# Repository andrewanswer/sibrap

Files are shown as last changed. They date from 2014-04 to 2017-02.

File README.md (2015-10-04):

СИБРАП - СИБИРСКАЯ РЕАЛИЗАЦИЯ РЕПРАП
31 марта 2012 - ...

О проекте
---------

Проект представляет собой 3D-принтер, позволяющий создавать
трехмерные объекты из пластика по его 3D-модели. Данный проект
был создан на базе проекта RepRap http://reprap.org и принтера Gen X
http://skb-kiparis.ru. Все файлы данного проекта выпущены под
лицензией GPL v3 (см. файл license_ru.txt).

Официальный сайт проекта - http://livelyminds.ru (Гибкие умы)

Об авторах
----------

Андрей Нуждов http://answe.ru
Будет дополняться...

Поддержка проекта
-----------------

Любой желающий поддержать проект анонимно либо публично может
перечислить любую сумму на следующие реквизиты:

Yandex.Money 4100171308229

WebMoney WMR R367868798166
         WMZ Z377208196018

Во втором случае он будет упомянут в списке жертвователей,
который будет включен в данный репозиторий проекта.

Развитие проекта
----------------

Все желающие помочь проекту делом, материалами или инструментами...
Если вы хотите открыть мастерскую, производящую Сибрапы, и вам
нужны консультации...
Если у вас есть вопросы и пожелания авторам...

пишите на http://livelyminds.ru/contact

==============================================================
SIBRAP - REPRAP SIBERIAN IMPLEMENTATION

About project
-------------

This project is a 3D-printer which allow to create real things
from plastic based on 3D-model. This project derived from RepRap
http://reprap.org and Gen X http://skb-kiparis.ru.
All this project files published under GPL v3 license
(see license_en.txt).

Official project site - http://livelyminds.ru (Lively Minds)

About authors
-------------

Andrew (Answer) Nuzhdov http://andrew.answer.name
Will be continued...

Project support
---------------

Anyone who want to support project (donate money) anonymously, or public,
can use next payment systems:

Yandex.Money 4100171308229

WebMoney WMR R367868798166
         WMZ Z377208196018

BitCoin  1qYeAD3AQgpYTpsLHjsZDKReWE29sTL8z
PayPal   andrew@answer.name

Second case sender will be included into list of donors
published in this repository.

Project expansion
-----------------

If you want to help project with any sort of activity, materials and tools...
If you try to open SibRaps foundry and want to consult...
Ii you have questions and wishes...

write to http://livelyminds.ru/contact

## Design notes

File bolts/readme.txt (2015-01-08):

BOLTS library have NUTS, WASHERS and HEX bolts, but doesn't exist bolts with cross-round head.
Here is it (MCAD OpenScad metric_fastners library used).

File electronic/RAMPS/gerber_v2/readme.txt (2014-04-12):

RAMPS_1-41.do  - Dimensions
RAMPS_1-41.GTL - TOP Copper
RAMPS_1-41.GBL - BOTTOM Copper
RAMPS_1-41.GTS - Solder stop mask Top
RAMPS_1-41.GBS - Solder stop mask Bottom
RAMPS_1-41.GTO - Silk Top
RAMPS_1-41.GBO - Silk Bottom
RAMPS_1-41.TXT - Drill

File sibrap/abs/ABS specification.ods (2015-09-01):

 |  |  | Часть принтера | Новое название |  | Название в sibrap_upgrade | Название в sibrap-kit | Кол-во деталей | Файл .scad | Файл .stl | Кол-во распечаток | Деталей внутри STL | Файл .gcode | Деталей внутри gcode
L | 1 | 4 | Каретка | carriage-part01 | x | Направляющие по оси Z | Направляющие (детали каретки X) | 1 | 1-rightbottom | 1-rightbottom | 1 | 1
L | 2 |  | Каретка | carriage-part02 | x |  |  | 1 | 2-leftbottom | 2-leftbottom | 1 | 1
L | 3 |  | Каретка | carriage-part03 | x |  |  | 1 | 3-righttop | 3-righttop | 1 | 1
L | 4 |  | Каретка | carriage-part04 | x |  |  | 1 | 4-lefttop | 4-lefttop | 1 | 1
S | 5 | 6 | Рама | frame-part01 | x | Зажим направляющих | Ушки | 4 | - | Зажим направляющих | 1 | 1
S | 6 |  | Рама | frame-part02 | x | Концевики | Крепления концевых датчиков | 3 | part23 | part23 | 3 | 1
S | 7 |  | Рама | frame-part03 | x | Прижим Z | Зажимы направляющих Z | 4 | part06 | part06 | 4 | 1
S | 8 |  | Рама | frame-part04 | x |  | Зависит от толщины рамы! | 4 | part06_1 | part06_1 | 4 | 1
S | 9 |  | Рама | frame-part05 | x | Хомут М5 | Хомуты М5 | 4 | - | Хомут М5 | 4 | 1
S | 10 |  | Рама | frame-part06 | x | Рама — Держатель кнопки | Печатать, только если нет в БП! | 1 | - | Держатель кнопки | 1 | 1
L | 11 | 8 | Головка-экструдер | head-part01 | x | Каретка экструдера | Головка экструдера | 1 | Экструдер_3_7 | Экструдер_3_7 | 1 | 1
M | 12 |  | Головка-экструдер | head-part02 | x | Экструдер — меньшая деталь | Головка экструдера | 1 | part18_new | part18_new | 1 | 1
S | 13 |  | Головка-экструдер | head-part03 | x | Экструдер — крышечка | Головка экструдера | 1 | part19 | part19 | 1 | 1
M | 14 |  | Головка-экструдер | head-part04 | x | Шестерни — большая (metal-bolt) | Редуктор большая шестерня | 1 | gear_large_42_teeth | gear_large_42_teeth | 1 | 1
S | 15 |  | Головка-экструдер | head-part05 | x | Шестерни — малая | Редуктор малая шестерня | 1 | gear_small_hole | gear_small_hole_4 | 1 | 1
S | 16 |  | Головка-экструдер | head-part06 | x | Каретка экструдера — шпуля 22 зуба | Натяжитель экструдера | 1 | Шпуля-GT2_22-зуба | Шпуля-GT2_22-зуба | 1 | 1
S | 17 |  | Головка-экструдер | head-part07 | x | Прижим разъема экструдера | Держатель разъема Molex | 1 | part16_molex | part16_molex | 1 | 1
S | 18 |  | Головка-экструдер | head-part08 | x | Прижим болта | Барашек | 1 | - | Барашек | 1 | 1
M | 19 | 5 | Катушка-вентилятор | holder-part01 | x | Держатель катушки | Держатель катушки | 2 | - | d3 | 2 | 1
M | 20 |  | Катушка-вентилятор | holder-part02 | x |  | Зависит от толщины рамы! | 1 | - | d2-v2 | 1 | 1
M | 21 |  | Катушка-вентилятор | holder-part03 | x |  | Зависит от толщины рамы! | 1 | - | d1-v3-rotated | 1 | 1
M | 22 |  | Катушка-вентилятор | holder-part04 | x | - | Крепление вентилятора | 1 | - | d5-v2 | 1 | 1
M | 23 |  | Катушка-вентилятор | holder-part05 | x |  | Зависит от толщины рамы! | 1 | - | d4-v2 | 1 | 1
M | 24 | 2 | Стол | table-part01 | x | Ножки | Ножки стола | 4 | part22 | part22 | 4 | 1
S | 25 |  | Стол | table-part02 | x | Зажимы ремня столика GT2 | Ремень стола | 9 | part12_gt2 | part12_gt2 | 3 | 3
 |  |  |  |  |  |  | Итого | 51
S — Small, M — Medium, L — Large
Постобработка деталей — сверла, диаметр
3 | 5 | 8 | base_plate01 | 1
3 |  |  | base_plate02 | 1
3 | 8 |  | base_plate03 | 1
4 | 5 | 8 | base_plate04 | 1
2 | 3 | 8 | carriage-part01 | 1
2 | 3 | 8 | carriage-part02 | 1
2 | 3 | 8 | carriage-part03 | 1
2 | 3 | 8 | carriage-part04 | 1
3 |  |  | head-part01 | 1
3 | 5 |  | head-part02 | 1
 |  |  | head-part04 | 1
 |  |  | ИТОГО | 11

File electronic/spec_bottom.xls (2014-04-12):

После заполнения спцификации, строки выделенные этим цветом желательно удалить, так как они не содержат необходимой для монтажа информации | Что необходимо предоставить при заказе на монтаж ПП
 | 1. Заполненный бланк заказа на монтаж
 | 2. Полный список комплектующих по заказу.( по Образцу)
 | 3. Список комплектующих по каждой стороне ПП: отдельно по SMD компонентам (с указанием типа корпуса )
 | и компонентам монтируемым в отверстия ПП. Наименование компонента в списке должно соответствовать
 | сборочному чертежу.
 | 4. На сборочном чертеже обязательно указать ориентацию полярных компонентов и микросхем.
 | 5. Сборочный чертеж должен быть понятен и хорошо читаем.
 | 6. При повторном заказе предоставлять список изменений.
Образец списка комплектующих |  | Ячейки выделенные желтым цветом обязательно заполнить
Организация | Название платы | Ответственное лицо, телефон |  | Кол-во плат
частное лицо | Плата 1984 | Нуждов А.А. 79232464120 |  | 50
Номинал | Позиционное обозначение | Тип | Дополнительная информация | Кол-во | Паек | Примечания
Компоненты для монтажа на поверхность
Резисторы
1.1 кОм | R1 | SMD 0805 | Резистор 0.125 W, SMD | 1 | 2
NTC 100 кОм | R2 | SMD 0805 | терморезистор 0.125 W, SMD | 1 | 2
Светодиоды
RED LED | D1 | SMD 0805 | Светодиод красный | 1 | 2
 |  |  | Всего SMD компонентов | 3
 |  |  | Всего паек SMD компонентов |  | 6
Компоненты для монтажа в отверстия
Разъемы
ножевая клемма на плату | J1-2 | TA-M | ножевая клемма | 2 | 4
2-pin угловой | X1 | MW-2MR | 2-pin угловой | 1 | 2
 |  |  | Всего монтир. в отверс. Компонентов | 3
 |  |  | Всего паек монт. в отв. компонентов |  | 6
Телефон: (383) 316-53-57 |  |  | E-mail: marlang@ngs.ru

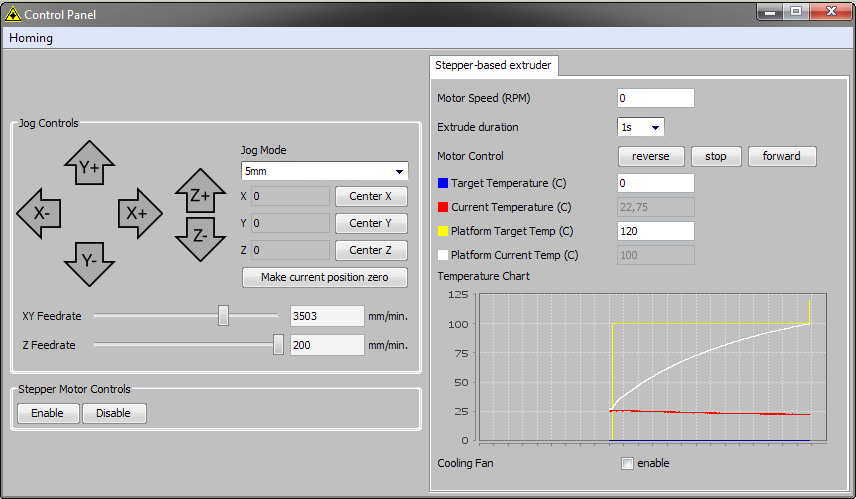
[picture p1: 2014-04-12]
electronic/kiparis-mytable.png

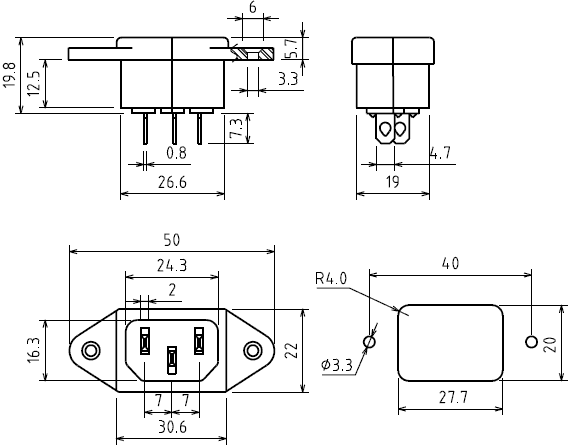
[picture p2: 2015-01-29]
specs/ac220v.gif

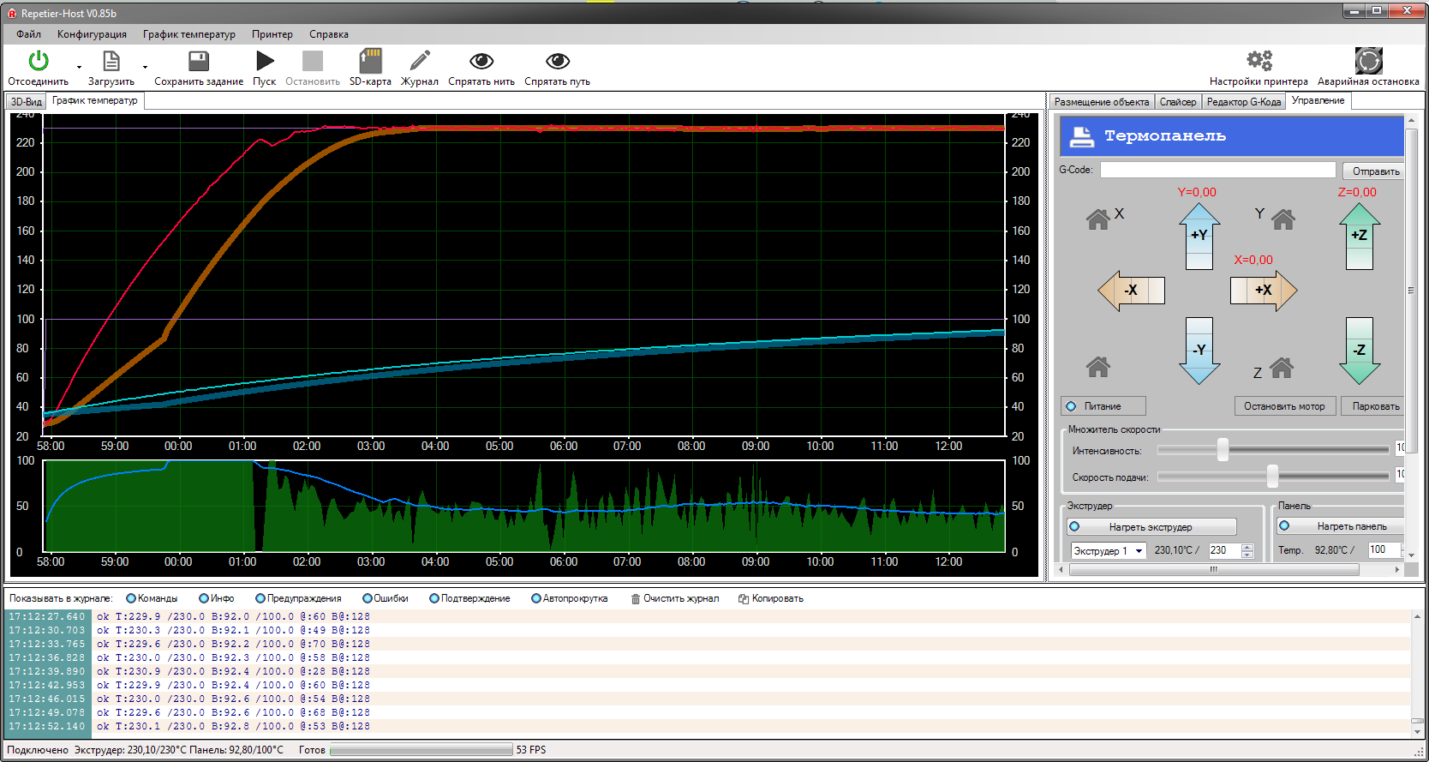
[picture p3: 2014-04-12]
electronic/ramps-mytable.png

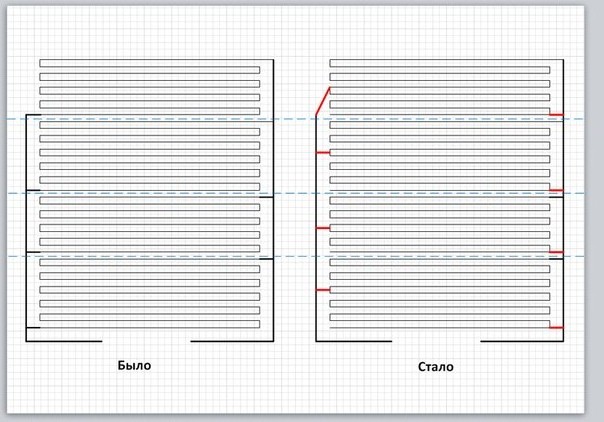
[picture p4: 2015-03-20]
electronic/table-update.jpg

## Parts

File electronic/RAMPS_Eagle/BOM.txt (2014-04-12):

Bill of Materials from RAMPS_1-41_n.sch, 88 parts, grouped by values, as of 21.06.2013 23:26:14

Part									Qty	Value			Device			Package			Description
5V, PS-ON, VCC								3	 			PINHD-1X1		1X01			Pin header 1x1 for 0.1" spacing
12V-AUX									1	 			M02PTH			1X02			Header 2
A-OUT, E0-MOT, E1-MOT, I2C, SERIAL, X-MOT, Y-MOT, Z-MOT, Z-MOT1		9	 			PINHD-1X4		1X04			PIN HEADER
C1, C5, C8								3	10uF			CPOL-US153CLV-0405	153CLV-0405		POLARIZED CAPACITOR, American symbol
C2									1	100nF			C-EUC0805		C0805			CAPACITOR, European symbol
C3, C4, C6, C7, C9, C10							6	100uF			CPOL-US153CLV-0605	153CLV-0605		POLARIZED CAPACITOR, American symbol
D1, D2									2	1N4004			1N4004			DO41-10			DIODE
F1									1	MFR500			PTCFUSE			MFR500			LITTLEFUSE
F2									1	MFR1100			PTCFUSEMFR1100		MFR1100			LITTLEFUSE
JP2, JP3, JP4, JP5, JP6							5	 			PINHD-2X3		2X03			PIN HEADER
JP7									1	 			M06SIP			1X06			Header 6
LED1, LED2, LED3, LED4							4	 			LEDCHIP-LED0805		CHIP-LED0805		LED
LOGO1									1	OSHW_LOGO_6MILX0100-NT	OSHW_LOGO_6MILX0100-NT	OSHW_6X100_NOTEXT
Q1, Q2, Q3								3	STP55NF06L		IRF512			TO220BV			N-CHANNEL MOS FET
R1, R7, R11, R21, R22							5	4.7K			R-US_R0805		R0805			RESISTOR, American symbol
R2, R3, R4, R5, R6, R8, R9, R10						8	100k			R-US_R0805		R0805			RESISTOR, American symbol
R12									1	1K			R-US_R0805		R0805			RESISTOR, American symbol
R13, R15								2	10r			R-US_R0805		R0805			RESISTOR, American symbol
R14									1	10r			R-US_M0805		M0805			RESISTOR, American symbol
R16, R17, R18, R19, R20							5	10k			R-US_R0805		R0805			RESISTOR, American symbol
R23, R24, R25								3	1.8K			R-US_R0805		R0805			RESISTOR, American symbol
S1									1	 			31-XX			B3F-31XX		OMRON SWITCH
SER1, SER2, SER3, SER4, X+, X-, Y+, Y-, Z+, Z-				10	 			3PIN-HEADER		3PIN-HEADER		PIN HEADER
U$2									1	282837-6		282837-6		282837-6
U$3									1	M04X2			M04X2			2X4
U$4, U$5, U$6, U$7, U$8							5	A4988BREAKOUT		A4988BREAKOUT		A4988BREAKOUT
U$9									1	M18_			M18_			1X18
U$10									1	M05X2			M05X2			2X5
U1									1	ARDUINO_MEGA_SHIELD	ARDUINO_MEGA_SHIELD	ARDUINO_MEGA_SHIELD
X4									1	MSTBA4			MSTBA4			MSTBA4			PHOENIX

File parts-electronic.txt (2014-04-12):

Электроника: поставщики

купили 21 ноября, доставили 25 ноября
Электронная плата основная 5000 р
Нагревательный элемент в сборе 1300 р
+ доставка через http://www.edostavka.ru 1000 р -

СКБ Кипарис http://skb-kiparis.ru
г.Москва, г.Зеленоград, корп. 1130
+7 (916) 754-99-29
+7 (926) 549-52-27
mail@skb-kiparis.ru

Разъемы, резисторы для нагревательного эл-та, разъем для подложки в
Радиотовары, Иванова, 17 (383) 336-05-26 http://novoelectronica.ru
(подложка - плата-теплый стол)

В начале ноября (примерно 3 ноября) ездили на оценку пр-ва электроники.
Оценка производства плат по файлам с разводкой -
Электроконнект, Инженерная, 4
(383) 336-10-01
(383) 336-10-03
order@pselectro.ru

Подложка:
10 шт = 8565 р
12 шт = 7980 р
24 шт = 11905 р

Gen6-электроника:
через калькулятор http://pselectro.ru/calc/
1 шт = 3269 р
10 шт = 4978 р
20 шт = 5714 р

реально, через беседу в офисе по макету
100 шт = 25000 р
10 шт = 7000 р
1 шт - ручная пайка = 10000 р
Контакт: Елена, (383) 316-53-57, marlang@ngs.ru

=====================================================
Элементы для подложки:
термистор
резистор
светодиод
=====================================================
Альтернативная электроника см REPRAP

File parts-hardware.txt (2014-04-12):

Железные детали, крепеж: поставщики

купили 7 ноября

Ремни Optibelt зубчатые
316XL 6,35 мм 4 шт * 158 р/шт + НДС 18% = 745 р
XL 6,35 мм 5 метров длиной, белый 1 шт * 1681 р + НДС 18% = 1983 р
Итого 2728 р, без доставки

Поставщик ЗИП-Балтика, Новосибирск
сайт http://e-zip.ru
(383) 325-34-12
(383) 233-05-11
(383) 325-34-13

купили 9 ноября

Двигатели 4 шт
Шаговый двигатель FL42STH38-1206A 4 шт * 928 р/шт + НДС 18% = 4380 р
+ доставка 1000 р = 5380 р

Поставщик ЗАО Меджик-Системс, Санкт-Петербург
сайт http://stepmotor.ru stepmotor@magicsys.spb.ru
(812) 327-13-88 доб 106
(812) 953-07-32
(812) 716-45-72

==============================================
Направляющие 6шт * 8мм диаметр * 400мм длиной выточил Владимир, обошлись в 1500 руб
Стержни 8мм с резьбой М8 можно купить в любом строительном магазине и нарезать их ножовкой
Все гайки, винты можно купить в магазине крепежа АкадемГородок ул. Иванова, 31 (383) 36-35-725
Латунный пруток для экструдера и нагревательного элемента купили в Бердске на пункте приема цветного металла
Фторопласт?
Подшипники?
Чертежи вручную выточенных деталей?
==============================================
Направляющие:
http://www.purelogic.ru/Netshop/linperem/cillinper/polival/ (от 10 мм)
http://electroprivod.ru/linear-guide-r.htm (на 8 мм есть но от 500 мм длины)
http://russian.alibaba.com/product-gs/standard-linear-shaft-8mm-540354747.html (Китай)
==============================================
Фторопласт, капролон (вместо бронзовых втулок можно сделать капролоновые)
http://www.rtigrupp.ru/ РЕЗИНОТЕХНИКА
(383) 363-27-01 (383) 363-27-02  ул. Толмачевская, 43/1
Там же можно купить гетинакс/стеклотекстолит для корпуса электроники
==============================================
Латунь
http://www.suet-metal.ru/cvetnoy-metal/latunnuy.htm
http://metacolor-nsk.ru/content/latun/
http://metalloprokat-scs.ru/czvetnoj-metall/latun-prokat/kvadrat-latunnyij.html
==============================================

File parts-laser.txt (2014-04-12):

Детали из оргстекла: поставщики, лазерная резка, файлы

19 октября
пришли детали для 3D принтера.
Файл parts-laser.cdr

оргстекло 665*322 мм, толщина 18 мм:
1 держатель маленький 24 шт
2 ножка-держатель 10 шт
3 загогулина верхняя 6 шт
4 держатель для мотора Z 5 шт
6 зажим для направляющей 8 шт
13 держатель для мотора Y 3 шт
17 каретка экструдера, самая большая деталь 3 шт
20 каретка площадки 2 шт

30 ноября
пришли детали для 3D принтера.
Файл parts2-laser.cdr (10 мм), остальное поштучно

оргстекло 180*180 мм, толщина 10мм:
16 большие шестерни экструдера 43 зуба 3 шт
10,11 шестерни на ось Z (справа и слева одинаковые) 8 шт

+ оргстекло 18мм, остатки предыдущего распила:
9 малые шестерни экструдера 10 зубов 3 шт
8 шестерни на ось X/Y 6 шт
5 держатели для концевиков 10 шт

========================================
Оргстекло (нужно 18 мм и 8 мм) можно купить тут
http://www.bis077.ru/catalog/goods/id/50255

ТД Пластик-Н ООО возле Автокомбината (Петухова Хилокский рынок)
г. Новосибирск, ул. Троллейная, д. 87 к4, оф. 2, эт. 2
тел. (383) 291-12-58 (383) 240-96-97
Оргстекло техническое, ТОСП, ТОСН, т.18мм, 1500х1700мм, литьевое, г. Новосибирск
Под заказ

18мм 1400x1620 15200 вес 60кг
раб время 9-17

Оргстекло техническое, ТОСП, ТОСН, т.8мм, 1500х1700мм, литьевое
5670 руб за лист, вес 26.5 кг
адрес? 

(звонить пн-пт 9-17)
или тут (www.termahim.ru/)
========================================
Нарезать можно тут
http://l-plast.ru/ (или http://www.siblaser.ru/)
(383)286-65-97 (383)299-68-10 Бердск, Линейная, 5/2

НО лучше всего тут Мазак Лазер т.к. по карте близко к ТД Пластик
лист можно повезти сразу к ним
http://www.m-lazer.ru/contacts/ ул. Сибиряков-Гвардейцев, 56 (383) 362-05-01

Кстати, лазерный б/у станок, который продается тут (http://l-plast.ru/ 9060SC) 
стоит относительно недорого -- новый стоит 200 тысяч 
http://cnc.ruprom.net/p39859-lazernyj-stanok-rabbit.html
Чаще всего выходит из строя лампа, стоит 20 тысяч
http://www.all-ready.ru/komplektuyuschie-lazernogo-oborudovaniya
========================================
Еще интересное наблюдение: схема бизнеса на 3д-принтерах в целом повторяет схему
бизнеса на лазерных станках:
1) продажа самих станков
2) продажа услуг по резке/печати
3) продажа продукции собственного изготовления (эксклюзивный дизайн вещи + резка/печать)

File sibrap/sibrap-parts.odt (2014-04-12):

Допилы деталей из оргстекла

Деталь 1 — держатель маленький

- развернуть отверстие на 8
- просверлить и развернуть перпендикулярное отверстие на высоте 7 от основания, симметрично осевой линии

Деталь 2 — ножка

- развернуть два отверстия на 8
- просверлить и развернуть два отверстия — в изогнутой верхней части на расстоянии 8 от края симметрично осевой линии, и на высоте 38 мм снизу симметрично осевой линии

Деталь 3 — загогулина верхняя

- развернуть два отверстия на 8
- просверлить и развернуть два отверстия — в изогнутой верхней части на расстоянии 9 от угла симметрично осевой линии

Деталь 4 — держатель для мотора Z

Две детали

4.1 — для двигателя. Нужно:

- высверлить 4 отверстия диаметром 3 для крепежа мотора
- нарезать резьбу М5 в двух отверстиях сбоку
- просверлить и развернуть два сквозных отверстия на 8 сбоку

4.2 — для держателя подшипника. Нужно:

- профрезеровать цилиндр под подшипник глубиной 7,6 мм и диаметром 22 мм
- нарезать резьбу М5 в 4х отверстиях для крепежа подшипника
- нарезать резьбу М5 в двух отверстиях сбоку
- просверлить и развернуть два сквозных отверстия на 8 сбоку

В случае двух двигателей нужны 2 детали 4.1

Деталь 5 — концевик

Деталь 6 — зажим для направляющей Z

- просверлить два отверстия диаметром 5 сбоку на расстоянии 16 друг от друга и симметрично осевой линии

Деталь 13 — держатель для мотора Y

Деталь 14 — держатель для мотора X

Деталь 15 — держатель каретки

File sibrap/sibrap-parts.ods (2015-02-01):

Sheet: SibRap 6
Принтер SibRap версия 6 (1.4)
Отличия:
 | - рама из 4х деталей (оргстекло 18мм)
 | - линейные подшипники LM8UU по всем осям вместо бронзовых втулок
 | - практически все 3д-печатные детали переделаны
 | - площадка под столом из алюминия вместо фанеры
 | - ремень Y теперь крепится иначе
 | - изменились длины шпилек и направляющих
 | - вместо муфт ставится резиновая трубка и хомуты
 | - по вертикали теперь шпилька М5
№ | Название | Хар-ки | Кол-во | Файл, примечания | Поставщик |  | Цена без учета доставки | Доставка | Примечание
1 | Двигатель | ST42-47 | 5
2 | Шкив ремня X,Y | На вал 5 мм, 20 зубов | 2
3 | Ремень зубчатый метражом | GT2 6,35 мм x 1,8 м | 1 | см. ниже расклад
4 | Направляющая | 400 мм длина, 8 мм диаметр | 4
4 | Направляющая | 434 мм длина, 8 мм диаметр | 2
5 | Линейные подшипники LM8UU | 8 внутр х 15 внеш х 24 длина | 12
6 | Шпилька резьбовая | М8, длина 324 мм | 4 | Рама
7 | Шпилька резьбовая | М5, длина 330 мм | 2 | Ходовые валы
 | Шпилька резьбовая | М8, длина 210 мм | 1 | Держатель катушки
 | Шпилька резьбовая | М8, длина 135 мм | 1 | Держатель катушки
 | Шпилька резьбовая | М8, длина 155 мм | 1 | Держатель катушки
8 | Рама из оргстекла | Оргстекло 18 мм | 1 | laser/frame/v2/blocks/frame_final
7 | Гайка с фланцем | М8 | 0 | см. ниже расклад
8 | Гайка обычная | М8 | 2 | см. ниже расклад
9 | Гайка удлиненная | М5 | 0 | см. ниже расклад
10 | Винт подшипника для ремня X | М8 х 30 | 2 | см. ниже расклад
11 | Шайбы обычные | М8 | 9 | см. ниже расклад
12 | Шайбы кузовные | М8 х 30 наружный диаметр | 6 | см. ниже расклад
13 | Винты с внутр шестигранником | М5 х 16 | 8 | см. ниже расклад
14 | Винты с внутр шестигранником, крепление корпуса | М5 х 10 | 8 | см. ниже расклад
15 | Винты для крепления площадки | М4 х 35 потайная | 4 | см. ниже расклад
16 | Гайки с сальником для площадки и сборки корпуса | М4 | 4 | см. ниже расклад
17 | Винт | М3 | 77 | см. ниже расклад
18 | Гайка | М3 | 55 | см. ниже расклад
19 | Винты для крепления корпуса | М4 х 10 полукруг крест | 12
20 | Корпус | Сталь 1,5 мм, 4 детали | 1
21 | Уголки | бытовые, 13мм до центров отверстий, диам отв 4 | 12
22 | Подшипник | 8 внутр х 22 внеш х 7 высота | 8 | см. ниже расклад
 |  |  |  | ftoroplast/
24 | Фторопластовая шайба |  | 1 | extruder-part01
25 | Фторопластовый термобарьер |  | 1 | extruder-part02
26 | Фторопластовый переходник 3 мм 1.75 мм |  | 1 | extruder-part07
 |  |  |  | metal/
27 | Нагревательный элемент | Латунь, 20х15х10 мм | 1 | extruder-part03
28 | П-швеллер | Алюминий, 20 (хвосты) х 25 (перекладина) х 36 мм (длина) | 1 | extruder-part04
29 | Латунное сопло |  | 1 | extruder-part05
30 | Болт с резьбовой канавкой | M8 x 60, резьба на хвосте 23 мм, шестигранная головка | 1 | extruder-part06
31 | Втулка для крышки головки | Алюминиевая трубка, диаметр 8, длина 12 мм | 1 | -
32 | Площадка под стол | Алюминий 3 мм | 1 | metal/alum_table/table-3mm-aluminium
33 | Радиатор | Алюминиевый охладитель — переделан |  | metal/alum_radiator
 |  |  |  | laser/
40 | Держатель для мотора Y | Оргстекло 8 мм | 1 | part13
41 | Держатель подшипника каретки | Оргстекло 8 мм | 1 | part14
42 | Держатель для мотора X | Оргстекло 8 мм | 1 | part15
 |  |  |  | abs/
44 | Держатель разъема | ABS-пластик, печатать слоем 0.3 мм | 1 | part16
45 | Головка, большая деталь | ABS-пластик, печатать слоем 0.3 мм | 1 | part17
46 | Головка, средняя деталь | ABS-пластик, печатать слоем 0.3 мм | 1 | part18
47 | Головка, крышечка | ABS-пластик, печатать слоем 0.3 мм | 1 | part19
48 | Держатель концевых переключателей | ABS-пластик, печатать слоем 0.3 мм | 3 | part23
49 | Втулка пластиковая для бронзовых втулок | ABS-пластик, печатать слоем 0.3 мм | 20 | part11
50 | Держатель ремня площадки | ABS-пластик, печатать слоем 0.3 мм | 6 | part12
51 | Редуктор, большая шестерня | ABS-пластик, печатать слоем 0.3 мм | 1 | gears/gear_large
52 | Редуктор, малая шестерня | нейлон, печатать слоем 0.3 мм | 1 | gears/gear_small
53 | Стекло | 210 х 210 х 4 мм с отшлифованными краями | 1
 |  |  |  | table/
54 | СМЛ стол | Стекломагниевый лист 210 x 210 x 8 мм, обклеен бумагой с помощью строительного клея ПВА | 1 | table2
56 | Концевые переключатели | 3-х позиционные микропереключатели | 3
57 | Набор электроники RAMPS | FreeDuino, 4 StepStick, RAMPS | 1
58 | Плата стола | Изготовлена, список компонентов см ниже | 1
59 | Блок питания ATX | LW2-500W | 1
60 | Кулер охлаждающий | 8 х 8 см | 1
61 | miniUSB-кабель | 1,8 м | 1
62 | Резистор для нагрева | 8 Ом 1 Вт | 2
63 | Термистор | EPCOS NTC 100 кОм, проволочно-стеклянный, диаметр 2 мм | 1
64 | Провода | Метраж и диаметр см ниже | 1
Метраж зубчатых ремней: на ось X — 90 см, на ось Y — 90 см.
Распил из 2х метровых шпилек M8: |  |  | Остаток, мм
1 | 324+324+324 | 972 | 28
2 | 324+210+135+155 | 824 | 176
Расклад крепежа:
Винты М8x30 с полукруглой головкой |  | Крепление подшипников ремня X | 2
Гайки М8 с фланцем:
4 | Крепление шпилек к раме | 4 | 16
2 | Крепление ушек | 4 | 8
1 | Крепление подшипников Y и детали part13 | 6 | 6
1 | Крепление подшипников X к деталям part14, part15 | 2 | 2
 |  | Итого | 32
Гайки М8 обычные:
1 | Крепление болта с канавкой к головке | 2 | 2
 |  | Итого | 2
Шайбы обычные M8:
4 | Для шкивов ремня Y
4 | Для шкивов ремня X
1 | Для большой шестерни на каретке
9 | Итого
Шайбы кузовные M8x30:
4 | Для шкивов ремня Y
2 | Для шкива ремня X
6 | Итого
Винты М5 с полукруглой головкой: |  | Длина, мм
2 | Сборка рамы | 50
2 | Сборка рамы | 60
Винты М5 с внутренним шестигранником: |  | Длина, мм
4 | Крепление направляющих Z | 35
4 | Крепление направляющих Z | 30
8 | Итого
Гайки M5 нейлон:
4 | Сборка рамы
8 | Крепление направляющих Z
12 | Итого
Гайки удлиненные M5:
2 | Ходовые гайки по Z
Шайбы М5:
4 | Сборка рамы
4 | Крепление направляющих Z
8 | Итого
Винты M4x35 потайная головка:
4 | Площадка стола
2 | Крепление вентилятора
6 | Итого
Гайки М4:
2 | Площадка стола | 4 | 8
2 | Крепление вентилятора | 1 | 2
 |  | Итого | 10
Гайки М4 нейлон:
1 | Площадка стола | 4 | 4
Шайбы M4:
3 | Площадка стола | 4 | 12
2 | Крепление вентилятора | 1 | 2
 |  | Итого | 14
Винты M3: |  | Длина, мм | Кол-во по длинам
4 | Крепление мотора X | 12 | 12 | 33
4 | Крепление мотора Y | 12 | 16 | 6
8 | Крепление моторов Z | 20 | 20 | 19
4 | Крепление мотора экструдера | 12 | 25 | 6
2 | Крепление скобы к мотору экструдера | 40/50 (зависит от мотора) | 30 | 3
1 | Крепление ремня X со стороны двигателя | 12 | 40 | 3
4 | Крепление линейных подшипников в каретке | 16 | 50 | 9
1 | Крепление ремня X со стороны головки | 16 | Итого | 79
3 | Крепление сопла к головке экструдера | 30
3 | Крепление головки к каретке | 50
1 | Прижим крышечки в головке экструдера | 16
4 | Крепление направляющих X (упор) | 12
8 | Крепление направляющих X (сжатие) | 20
16 | Крепление ножек к площадке стола | 12
3 | Крепление держателя концевых переключателей | 20
6 | Крепление ремня Y к столу | 25
4 | Крепление каретки XZ | 50
1 | Натяжитель ремня в столе | 40
77 | Итого
Гайки М3:
4 | Крепление линейных подшипников в каретке
2 | Крепление ремня X со стороны головки
3 | Крепление сопла к головке экструдера
3 | Крепление головки к каретке
1 | Прижим крышечки в головке экструдера
12 | Крепление направляющих X
16 | Крепление ножек к площадке стола
3 | Крепление держателя концевых переключателей
6 | Крепление ремня Y к столу
4 | Крепление каретки XZ
1 | Натяжитель ремня в столе
55 | Итого
Шайбы M3:
1 | Прижим крышечки в головке экструдера
8 | Крепление направляющих X
16 | Крепление ножек к площадке стола
3 | Крепление держателя концевых переключателей
6 | Крепление ремня Y к столу
8 | Крепление каретки XZ
1 | Натяжитель ремня в столе
43 | Итого
Винты М2:
6 | Крепление концевых переключателей
Гайки M2:
6 | Крепление концевых переключателей
Подшипники:
4 | Каретка экструдера
2 | Шкив ремня Y
2 | Шкив ремня X
8 | Итого
Длины проводов: |  | Длина, мм | Кол-во жил | Сечение жилы, мм2 | Кол-во выводов на разъемы RAMPS | Кол-во выводов на клеммы RAMPS
 | Концевик X | 600 | 2 | 0,35 | 2 | 0
 | Концевик Y | 700 | 2 | 0,35 | 2 | 0
 | Концевик Z | 600 | 2 | 0,35 | 2 | 0
 | Кулер | 600 | 2 | 0,35 | 0 | 2
 | Мотор X | 400 | 4 | 0,35 | 4 | 0
 | Мотор Y | 500 | 4 | 0,35 | 4 | 0
 | Мотор Z1 (над X) | 200 | 4 | 0,35 | 4 | 0
 | Мотор Z2 | 400 | 4 | 0,35 | 4 | 0
 | Мотор E | 900 | 4 | 0,35 | 4 | 0
 | Сопло S | 1100 | 4 | 0,35 | 2 | 2
 | От сопла до разъема | 100 | 4 | 0,35 | 0 | 0
в наборе | Стол датчик | 900 | 2 | 0,35 | 2 | 0
в наборе | Стол нагрев | 800 | 2 | 2,5 | 0 | 2
есть в БП | Блок питания | 450 | 4 | 0,35 | 0 | 4
 |  |  |  |  | 30 | 10
Итого |  | в принтере |  | в наборе
2-жильный 0,35 мм2 |  | 3400 | т. е. 4 метра | 2500 | т. е. 3 метра
2-жильный 2,5 мм2 |  | 800 | т. е. 1 метр | 0
4-жильный 0,35 мм2 |  | 3500 | т. е. 4 метра | 3500 | т. е. 4 метра
Это берется из БП:
в наборе | Разъем питания сопла | 4х1 мама | 1
 |  |  |  |  | Длины проводов приведены с учетом 300 мм хвостов у моторов и 400 мм хвоста у кулера.
 |  |  |  |  | (проверяйте длину проводов моторов, т. к. она у разных моделей разная)
 |  |  |  |  | Рекомендуется нагрузить шину +5В у блока питания (дает +5% эффективности)
Это покупается:
 | Термоусадка 2 мм | 1 м | 1
 | Термоусадка 7 мм | 5 м | 1
подробнее по разъемам написано тут
wiki.livelyminds.ru/w/Сборка_электроники_SibRap

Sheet: SibRap 5
Принтер SibRap версия 5 (1.1)
Отличия:
 | - моторы перенесены вниз
 | - добавлены новые детали из оргстекла (part07 на ось Z)
 | - переделана part13 (крепление мотора Y)
 | - детали переименованы
 | - редуктор теперь напечатан из ABS+нейлон
 | - в редукторе шевронная шестерня
 | - перешли на ремень GT2 и заводские шкивы GT2 (аналогов в России не нашли)
 | - провода оптимизированы
 | - по Y ремень перекручен мебиусом
№ | Название | Хар-ки | Кол-во | Файл, примечания | Поставщик | Цена без учета доставки | Доставка | Примечание
1 | Двигатель | ST42-47 | 5 |  | Даркстон
2 | Шкив ремня X,Y | На вал 5 мм, 20 зубов | 2 |  | Ниоз
3 | Ремень зубчатый метражом | GT2 6,35 мм x 1,8 м | 1 | см. ниже расклад | Ниоз
4 | Направляющая | 400 мм длина, 8 мм диаметр | 4 |  | Даркстон
4 | Направляющая | 440 мм длина, 8 мм диаметр | 2 |  | Даркстон
5 | Втулка бронзовая | 8 внутр х 11.5 внеш х 10.5 длина | 12 |  | БиосСет
6 | Шпилька резьбовая | М8, длина 430 мм | 4 | см. ниже расклад | Крепеж
6 | Шпилька резьбовая | М8, длина 370 мм | 6 |  | Крепеж
6 | Шпилька резьбовая | М8, длина 350 мм | 2 |  | Крепеж
6 | Шпилька резьбовая | М8, длина 300 мм | 4 |  | Крепеж
7 | Гайка с фланцем | М8 | 88 | см. ниже расклад | Крепеж (Иванова, 31)
8 | Гайка обычная | М8 | 2 | см. ниже расклад | Крепеж
9 | Гайка удлиненная | М8 | 7 | см. ниже расклад | Крепеж
10 | Винт подшипника для ремня X | М8 х 30 | 2 |  | Крепеж
11 | Шайбы обычные | М8 | 8 | см. ниже расклад | Крепеж
12 | Шайбы кузовные | М8 х 30 наружный диаметр | 6 | см. ниже расклад | Крепеж
13 | Винты с внутр шестигранником | М5 х 16 | 16 | см. ниже расклад | Крепеж
14 | Винты с внутр шестигранником, крепление корпуса | М5 х 10 | 8 | см. ниже расклад | Крепеж
15 | Винты для крепления площадки | М4 х 35 потайная | 4 |  | Крепеж
16 | Гайки с сальником для площадки и сборки корпуса | М4 | 36 | см. ниже расклад | Крепеж
17 | Винт | М3 | 58 | см. ниже расклад | Крепеж
18 | Гайка | М3 | 34 | см. ниже расклад | Крепеж
19 | Винты для крепления корпуса | М4 х 10 полукруг крест | 12 |  | Крепеж
20 | Корпус | Сталь 1,5 мм, 4 детали | 1 |  | БиосСет
21 | Уголки | бытовые, 13мм до центров отверстий, диам отв 4 | 12 |  | Крепеж
22 | Подшипник | 8 внутр х 22 внеш х 7 высота | 10 | см. ниже расклад | АкадемСнаб (Пасечная, 4)
23 | Муфта для двигателей оси Z | Алюминий, разрезная, вал 5 x резьба M8 | 2 |  | Даркстон
 |  |  |  | ftoroplast/
24 | Фторопластовая шайба |  | 1 | extruder-part01 | БиосСет
25 | Фторопластовый термобарьер |  | 1 | extruder-part02 | БиосСет
26 | Фторопластовый переходник 3 мм 1.75 мм |  | 1 | extruder-part07 | БиосСет
 |  |  |  | metal/
27 | Латунный нагревательный элемент |  | 1 | extruder-part03 | Виталий, НГТУ
28 | П-швеллер | Алюминий, 20 (хвосты) х 25 (перекладина) х 36 мм (длина) | 1 | extruder-part04 | Леруа Мерлен
29 | Латунное сопло |  | 1 | extruder-part05 | Евгений
30 | Болт с резьбовой канавкой | M8 x 60, резьба на хвосте 23 мм, шестигранная головка | 1 | extruder-part06
31 | Втулка для крышки головки | Алюминиевая трубка, диаметр 8, длина 12 мм | 1 | - | Леруа Мерлен
 |  |  |  | laser/
32 | Держатель маленький | Оргстекло 18 мм | 8 | part01 | Л-Пласт (Бердск, Линейная, 5/2)
33 | Ножка | Оргстекло 18 мм | 4 | part02
34 | Загогулина верхняя | Оргстекло 18 мм | 2 | part03
35 | Держатель для мотора Z | Оргстекло 18 мм | 2 | part04
36 | Держатель для ведомого вала Z | Оргстекло 18 мм | 2 | part05
37 | Зажим для направляющей Z | Оргстекло 18 мм | 4 | part06
38 | Детали каретки (2 основных + 2 зеркальных) | Оргстекло 18 мм | 4 | part07
39 | Ножка площадки | Оргстекло 18 мм | 4 | part22
40 | Держатель для мотора Y | Оргстекло 8 мм | 1 | part13
41 | Держатель подшипника каретки | Оргстекло 8 мм | 1 | part14
42 | Держатель для мотора X | Оргстекло 8 мм | 1 | part15
43 | Держатель подшипника вала Z | Оргстекло 8 мм | 2 | part21
 |  |  |  | abs/
44 | Держатель разъема | ABS-пластик, печатать слоем 0.3 мм | 1 | part16 | Пластик из Нижнего Новгорода
45 | Головка, большая деталь | ABS-пластик, печатать слоем 0.3 мм | 1 | part17
46 | Головка, средняя деталь | ABS-пластик, печатать слоем 0.3 мм | 1 | part18
47 | Головка, крышечка | ABS-пластик, печатать слоем 0.3 мм | 1 | part19
48 | Держатель концевых переключателей | ABS-пластик, печатать слоем 0.3 мм | 3 | part23
49 | Втулка пластиковая для бронзовых втулок | ABS-пластик, печатать слоем 0.3 мм | 20 | part11
50 | Держатель ремня площадки | ABS-пластик, печатать слоем 0.3 мм | 6 | part12
51 | Редуктор, большая шестерня | ABS-пластик, печатать слоем 0.3 мм | 1 | gears/gear_large
52 | Редуктор, малая шестерня | нейлон, печатать слоем 0.3 мм | 1 | gears/gear_small
53 | Стекло | 210 х 210 х 4 мм с отшлифованными краями | 1 |  | Фортуна (Иванова, 31)
 |  |  |  | table/
54 | СМЛ стол | Стекломагниевый лист 210 x 210 x 8 мм, обклеен бумагой с помощью строительного клея ПВА | 1 | table2 | Леруа Мерлен
55 | Подставка под стол | Фанера 180 x 120 x 6 мм | 1 | table1 | Валерий (+79139061538)
56 | Концевые переключатели | Микрокнопки | 3 |  | Радиотехника (Иванова, 17)
57 | Набор электроники RAMPS | FreeDuino, 4 StepStick, RAMPS | 1 |  | Девиктер
58 | Плата стола | Изготовлена, список компонентов см ниже | 1 |  | Электроконнект
59 | Блок питания ATX | LW2-500W | 1 |  | e2e4online (ВЦ)
60 | Кулер охлаждающий | 8 х 8 см | 1 |  | Квеста (Пентагон)
61 | miniUSB-кабель | 1,8 м | 1 |  | Квеста
62 | Резистор для нагрева | 8 Ом 2 Вт | 2 |  | Радиотехника
63 | Термистор | EPCOS NTC 100 кОм, проволочно-стеклянный, диаметр 2 мм | 1 |  | Элитан
64 | Провода | Метраж и диаметр см ниже | 1 |  | Радиотехника
Метраж зубчатых ремней: на ось X — 90 см, на ось Y — 90 см.
Распил из 7 метровых шпилек: |  |  | Остаток, см |  | Общий метраж:
1 | 43+37 | 80 | 20 |  | 43 | 4 | 172
2 | 43+37 | 80 | 20 |  | 37 | 6 | 222
3 | 43+37 | 80 | 20 |  | 35 | 2 | 70
4 | 43+37 | 80 | 20 |  | 30 | 4 | 120
5 | 30+30+37 | 97 | 3 |  |  |  | 584
6 | 30+30+37 | 97 | 3
7 | 35+35 | 70 | 30
Гайки М8 с фланцем:
8 | Держатель маленький | 2 | 16
4 | Ножка | 8 | 32
2 | Загогулина верхняя | 8 | 16
2 | Держатель для мотора Z | 4 | 8
2 | Держатель для ведомого вала Z | 4 | 8
4 | Зажим для направляющей Z | 0 | 0
4 | Детали каретки (2 основных + 2 зеркальных) | 0 | 0
4 | Ножка площадки | 0 | 0
1 | Держатель для мотора Y | 4 | 4
1 | Держатель подшипника каретки | 1 | 1
1 | Держатель для мотора X | 1 | 1
2 | Держатель подшипника вала Z | 0 | 0
1 | Крепление подшипника Y напротив мотора | 2 | 2
 |  | Итого | 88
Гайки М8 обычные:
2 | Крепление подшипников Z | 1 | 2
 |  | Итого | 2
Гайки удлиненные M8:
4 | Ходовые гайки по Z | 1 | 4
2 | Крепление подшипников Z | 1 | 2
1 | Крепление болта с канавкой к головке | 1 | 1
 |  | Итого | 7
Шайбы обычные M8:
4 | Для шкивов ремня Y
4 | Для шкивов ремня X
8 | Итого
Шайбы кузовные M8x30:
4 | Для шкивов ремня Y
2 | Для шкива ремня X
6 | Итого
Винты M3: |  | Длина, мм | Кол-во по длинам
4 | Крепление мотора X | 12 | 12 | 13
4 | Крепление мотора Y | 12 | 16 | 18
8 | Крепление моторов Z | 20 | 20 | 11
4 | Крепление мотора экструдера | 12 | 25 | 4
1 | Крепление ремня X со стороны двигателя | 12 | 30 | 3
1 | Крепление ремня X со стороны головки | 16 | 50 | 9
3 | Крепление сопла | 30 | Итого | 58
3 | Крепление головки экструдера | 50
1 | Прижим крышечки в головке экструдера | 16
8 | Крепление направляющих X | 16
8 | Крепление ножек к площадке стола | 16
3 | Крепление держателя концевых переключателей | 20
4 | Крепление ремня Y к столу | 25
2 | Крепление скобы к мотору экструдера | 50
4 | Крепление каретки XZ | 50
58 | Итого
Винты M4 потайная головка: |  | Длина, мм
4 | Площадка стола | 35
Гайки М4 с сальником:
4 | Площадка стола | 3 | 12
12 | Сборка корпуса | 2 | 24
 |  | Итого | 36
Гайки М3:
3 | Крепление головки экструдера
3 | Крепление головки к каретке
1 | Прижим крышечки в головке экструдера
8 | Крепление направляющих X
8 | Крепление ножек к площадке стола
3 | Крепление держателя концевых переключателей
4 | Крепление ремня Y к столу
4 | Крепление каретки XZ
34 | Итого
Винты М5 с внутренним шестигранником: |  | Длина, мм
8 | Крепление подшипников Z | 16
8 | Крепление направляющих Z | 16
8 | Крепление корпуса | 10
24 | Итого
Подшипники:
4 | Каретка экструдера
2 | Шкив ремня Y
2 | Шкив ремня X
2 | Валы по Z
10 | Итого
Длины проводов: |  | Длина, мм | Кол-во | Итого, мм | Двухжильные провода? | Кол-во выводов на разъемы RAMPS | Кол-во выводов на клеммы RAMPS
 | Концевик X | 600 | 1 | 600 | Да, 0,35 мм2 | 2 | 0
 | Концевик Y | 700 | 1 | 700 | Да, 0,35 мм2 | 2 | 0
 | Концевик Z | 600 | 1 | 600 | Да, 0,35 мм2 | 2 | 0
 | Мотор X | 400 | 2 | 800 | Да, 0,35 мм2 | 4 | 0
 | Мотор Y | 500 | 2 | 1000 | Да, 0,35 мм2 | 4 | 0
 | Мотор Z1 (над X) | 150 | 2 | 300 | Да, 0,35 мм2 | 4 | 0
 | Мотор Z2 | 400 | 2 | 800 | Да, 0,35 мм2 | 4 | 0
 | Мотор E | 900 | 2 | 1800 | Да, 0,35 мм2 | 4 | 0
 | Сопло S | 1100 | 2 | 2200 | Да, 0,35 мм2 | 2 | 2
 | Кулер | 600 | 1 | 600 | Да, 0,35 мм2 | 0 | 2
 | Стол датчик | 900 | 1 | 900 | Да, 0,35 мм2 | 2 | 0
 | От сопла до разъема | 150 | 2 | 300 | Да, 0,35 мм2 | 0 | 0
 | Стол нагрев | 800 | 1 | 800 | Да, 2,5 мм2 | 0 | 2
 | Блок питания | 450 | 2 | 900 | Да, 2,5 мм2 | 0 | 4
Итого |  |  |  |  |  | 30 | 10
2жильный 0,35 мм2 |  | 10600 | или 11 м
2жильный 2,5 мм2 |  | 1700 | или 2 м |  | Т.к. провод красно-черный, расклад на моторы идет такой:
 |  |  |  |  | красный | Красный 1
Это берется из БП: |  |  |  |  | синий | Черный 1
 | Разъем питания сопла | 4х1 мама | 1 |  | зеленый | Красный 2
 |  |  |  |  | черный | Черный 2
Это покупается: |  |  |  |  | Длины проводов приведены с учетом 300 мм хвостов у моторов и 400 мм хвоста у кулера.
 | Линейка PBS-40 |  | 1
 | Ответный разъем стола CHU-2 |  | 1 |  | Рекомендуется нагрузить шину +5В у блока питания (дает +5% эффективности)
 | Ответные клеммы стола 36063LB |  | 2
 | Угловой разъем THP-4MR (4x1 папа) |  | 1
 | Термоусадка 2 мм2 | 1 м | 1
подробнее по разъемам написано тут
wiki.livelyminds.ru/w/Сборка_электроники_SibRap

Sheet: SibRap 3
Принтер SibRap версия 3
Отличия:
 | - добавлен подшипник на каретку рядом с мотором X
 | - добавлены заводские муфты на ось Z
 | - добавлен мотор на ось Z
 | - ходовые и упорные гайки по Z заменены на удлиненные
 | - ходовые шпильки зафиксированы в подшипниках сверху и снизу
 | - шестигранник в шестерне подачи пластика теперь из металла (гайка с фланцем со срезанной резьбой)
 | - немного изменена форма некоторых деталей каретки
 | - добавлены новые детали из оргстекла (копии деталей part04, part05, part06, part21 на ось Z)
 | - шпилек теперь нужно всех размеров (30,37,43) по 6 шт
 | - part21 необходимо сточить до 7 мм в высоту
 | - втулки вновь бронзовые
№ | Название | Хар-ки | Кол-во | Файл, примечания | Поставщик | Цена без учета доставки | Доставка | Примечание
1 | Двигатель | FL42 STH38-1206A | 5 |  | Степ-Мотор | 4380 | 1000
2 | Ремень зубчатый кольцевой | Optibelt 316XL 6,35 мм | 1 |  | ЗИП-Балтика | 200 | 0
3 | Ремень зубчатый метражом | Optibelt XL 6,35 мм x 2 м | 1 |  | ЗИП-Балтика | 800 | 0
4 | Направляющая | 400 мм длина, 8 мм диаметр | 6 |  | Владимир | 1000 | 0
5 | Втулка бронзовая | 8 внутр х 11.5 внеш х 10.5 длина | 12 |  | Владимир | 500 | 0
6 | Шпилька резьбовая | М8, длина 430 мм | 3 |  | Абрис | 270 | 0
7 | Шпилька резьбовая | М8, длина 370 мм | 6 |  | Абрис
8 | Шпилька резьбовая | М8, длина 300 мм | 5 |  | Абрис
9 | Шпилька резьбовая | М8, длина 270 мм | 1 |  | Абрис
10 | Гайка с фланцем | М8 | 84 |  | Крепеж (Иванова, 31)
11 | Гайка обычная | М8 | 4 | ходовая гайка по Z | Крепеж
12 | Гайка со стопорным кольцом | М8, крепление шкивов Z | 10 |  | Крепеж
13 | Винт подшипника для ремня X | М8 х 30 | 1 |  | Крепеж
14 | Шайбы обычные | М8 | 7 |  | Крепеж
15 | Шайбы кузовные | М8 х 30 наружный диаметр | 5 | шкивы X, Y | Крепеж
16 | Шайбы кузовные Z | М8 х 40 наружный диаметр | 4 | шкивы Z | Крепеж
17 | Винты под шестигранный ключ | М5 х 16 | 8 |  | Крепеж
18 | Винт | М3 | 44 | см. ниже деталировку по длинам | Крепеж
19 | Гайка | М3 | 27 |  | Крепеж
20 | Винты для крепления площадки | М4 х 35 | 4 |  | Крепеж
21 | Гайки с сальником для площадки | М4 | 12 |  | Крепеж
22 | Винты для крепления концевых переключателей | М2 х 10 | 6 |  | Крепеж
23 | Подшипник | 8 внутр х 22 внеш х 7 высота | 7 |  | АкадемСнаб (Пасечная, 4) | 385
24 | Фторопластовая трубка |  | 1 | extruder-part02 | Леша
25 | Фторопластовая шайба |  | 1 | extruder-part01 | Леша
26 | Латунное сопло |  | 1 | extruder-part12 | Евгений
27 | Латунный нагревательный элемент |  | 1 | extruder-part13 | Кипарис | 1300 | 1000
28 | Болт с резьбовой канавкой | M8 x 60, резьба на хвосте 23 мм, шестигранная головка | 1 | part22 | Евгений
29 | Шайба для шкива Z | Металл | 2 | part10_1 деталь 2 | Леша
30 | Шкив Z ведущий | Металл | 1 | part10_1 деталь 1 | Леша
31 | Шкив Z ведомый | Металл | 1 | part11_1 деталь 1 | Леша
32 | П-швеллер | Алюминий, 20 (хвосты) х 25 (перекладина) х 35 мм (длина) | 1 | extruder-part04 | Леруа Мерлен (Дима)
33 | Втулка для крышки головки | Алюминиевая трубка, диаметр 8, длина 10 мм | 1 |  | Леруа Мерлен
34 | Держатель маленький | Оргстекло 18 мм | 8 | part01 | Л-Пласт (Бердск, Линейная, 5/2) | 2500 |  | оргстекло свое, узнать цены
35 | Ножка | Оргстекло 18 мм | 4 | part02
36 | Загогулина верхняя | Оргстекло 18 мм | 2 | part03
37 | Держатель для мотора Z | Оргстекло 18 мм | 1 | part04
38 | Держатель для ведомого вала Z | Оргстекло 18 мм | 1 | part05
39 | Зажим для направляющей Z | Оргстекло 18 мм | 2 | part06
40 | Шестерня на вал двигателя X,Y | Оргстекло 18 мм | 2 | part08
41 | Шестерня на вал двигателя экструдера | Оргстекло 18 мм | 1 | part09
42 | Шестерня для шкивов оси Z | Оргстекло 8 мм | 2 | part10
43 | Держатель для мотора Y | Оргстекло 8 мм | 1 | part13
44 | Держатель для мотора X | Оргстекло 8 мм | 1 | part14
45 | Держатель подшипника каретки | Оргстекло 8 мм | 1 | part15
46 | Шестерня подачи пластика | Оргстекло 8 мм | 1 | part16
47 | Держатель подшипника вала Z | Оргстекло 8 мм | 1 | part21
48 | Муфта переходная для оси Z из 2х частей (крестовина?) | Оргстекло 8 мм | 1 | part22
49 | Головка из 3х частей | Пластик, печатать слоем 0.4 мм | 1 | part17, part18, part19 | Пластик из Нижнего Тагила
50 | Детали каретки, 4 части | Пластик, печатать слоем 0.4 мм | 1 | part15_2 x 2, part15_3 x 2
51 | Держатель площадки | Пластик, печатать слоем 0.4 мм | 4 | part20_1
52 | Втулка пластиковая шестигранная | Пластик, печатать слоем 0.2 мм | 1 | part16_1
53 | Втулка пластиковая для бронзовых втулок | Пластик, печатать слоем 0.2 мм | 12 | part17_1
54 | Держатель концевых переключателей | Пластик, печатать слоем 0.4 мм | 3 | part05
55 | Держатель ремня площадки | Пластик, печатать слоем 0.2 мм | 2 | part20_2
56 | Стекло | 210 х 210 х 4 мм с отшлифованными краями | 1 |  | Фортуна (Иванова, 31) | 75 | 0
57 | СМЛ площадка | Стекломагниевый лист 210 x 210 x 6 мм, обклеен бумагой с помощью строительного клея ПВА | 1 |  | Леруа Мерлен | 260 | 0
58 | СМЛ подставка под площадку | Стекломагниевый лист 180 x 120 x 6 мм, обклеен бумагой с помощью строительного клея ПВА | 1 |  | Леруа Мерлен
59 | Концевые переключатели |  | 3 |  | Радиотехника (Иванова, 17) | 6 | 0
60 | Плата электроники |  | 1 |  | Кипарис | 5000 | 1000
61 | Теплый стол |  | 1 |  | Кипарис | 1500 | 1000
62 | Блок питания ATX | LW2-500W | 1 |  | Техносити (ВЦ) | 860 | 0
63 | Кулер охлаждающий | 8 х 8 см | 1 |  | Квеста (Пентагон) | 50
64 | Шнур питания |  | 1 |  | Квеста | 90 | 0
65 | USB-кабель |  | 1 |  | Квеста | 60 | 0
66 | Разъем для двигателей | 4 х 1, мама, + 4 контакта | 4 |  | Радиотовары (Зыряновская, 119)
67 | Разъем для кулера | 3 х 1, мама, + 3 контакта | 1 |  | Радиотовары
68 | Разъем питания платы 2 | 3 х 2, мама, + 6 контактов | 1 |  | Радиотовары
69 | Разъем для концевых переключателей 3x1 | 3 х 1, мама, + 3 контакта | 3 |  | Радиотовары
70 | Резистор для нагрева | 4 Ом 1 Вт | 2 |  | Радиотехника
71 | Термистор | NTC 56 кОм, проволочно-стеклянный, диаметр 2 мм | 1 |  | Кипарис
72 | Провод толстый 1 м | Медный двужильный в силиконовой изоляции сечением 2,5 мм2 | 1 |  | Радиотехника | 57
73 | Реле | №19 СМА3-1U (12VDC-40A) | 1 |  | Радиотехника | 65
74 | Диод | 1.5 КЕ 200 А | 1 |  | Радиотехника | 18
Это берется из БП:
 | Разъем питания стола и нагревательного элемента | 2 х 2, мама | 2
 | Разъем питания платы 1 | 4 х 1, мама | 1
Распил из 6 метровых шпилек: |  |  | Остаток, см
1 | 43+37 | 80 | 20
2 | 43+37 | 80 | 20
3 | 43+37 | 80 | 20
4 | 30+30+37 | 97 | 3
5 | 30+30+37 | 97 | 3
6 | 30+30+37 | 97 | 3
Гайки М8:
8 | На каждую ножку и верхнюю загогулину | 6 | 48
4 | Крепление мотора Z и ведомого вала | 2 | 8
6 | Горизонтальная шпилька по центру внизу | 2 | 12
2 | Крепление направляющих Y | 4 | 8
6 | Крепление мотора Y и шкивов | 1 | 6
1 | Крепление подшипника для ремня X | 1 | 1
1 | Крепление болта с канавкой | 1 | 1
 |  | Итого | 84
Винты M3: |  | Длина, мм | Кол-во по длинам
4 | Крепление мотора X | 12 | 12 | 5
4 | Крепление мотора Y | 20 | 16 | 18
4 | Крепление мотора Z | 20 | 20 | 11
1 | Крепление ремня X со стороны двигателя | 12 | 25 | 7
1 | Крепление ремня X со стороны головки | 16 | 45 | 3
3 | Крепление сопла | 25 | Итого | 44
3 | Крепление головки экструдера | 45
1 | Прижим крышечки в головке экструдера | 16
8 | Крепление направляющих X | 16
8 | Крепление площадки | 16
3 | Крепление держателя концевых переключателей | 20
4 | Крепление ремня Y | 25
44 | Итого
Гайки М3:
3 | Крепление головки экструдера
1 | Прижим крышечки в головке экструдера
8 | Крепление направляющих X
8 | Крепление площадки
3 | Крепление держателя концевых переключателей
4 | Крепление ремня Y
27 | Итого
Подшипники:
4 | Каретка экструдера
2 | Шкив ремня Y
1 | Шкив ремня X
7 | Итого
Шайбы обычные:
4 | Для шкивов ремня Y
2 | Для шкива ремня X
1 | Для болта экструдера
7 | Итого
Шайбы кузовные:
4 | Для шкивов ремня Y
1 | Для шкива ремня X
5 | Итого
Винты М5:
4 | Крепление ведомого вала Z
4 | Крепление направляющих Z
8 | Итого
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

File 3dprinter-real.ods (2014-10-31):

Дата | День недели | Получил | Откуда | Где | Потратил | На что | Где
20.07.2011 | среда |  |  |  | 49700 | Оплата 3D-принтера через WU | Глобэкс-банк
26.07.2011 | вторник |  |  |  | 1600 | Весы Tefal | РемБытТехника
29.07.2011 | пятница |  |  |  | 291 | Две отвертки, плоскогубцы, наждачка | Дюжина
30.07.2011 | суббота |  |  |  | 100 | Суперклей, ацетон | Магазин Строитель
03.08.2011 | среда | 300 | Продажа 3х моделей машинок
08.09.2011 | четверг |  |  |  | 1000 | Штангенциркуль электронный | Мастер-инструмент, Арбузова, 10
14.09.2011 | среда |  |  |  | 20 | Болты с гайками 10 шт | Магазин ПТУ-55
27.09.2011 | вторник | 5500 | Получено от Наговицина Владимира на пластик
28.09.2011 | среда |  |  |  | 11000 | Пластик для принтера (ABS, 20 кг, красный+желтый) | Группа компаний Лираль
01.10.2011 | суббота |  | переселился на работу + бизнес в офис БЦ Петербург
09.11.2011 | среда |  |  |  | 15 | Разъемы | Магазин Радиотовары, Иванова, 17
30.01.2012 | понедельник |  |  |  | 2000 | Наговицину в счет долга | Щ
03.02.2012 | пятница | 1500 | Печать модели для Adaptica
 |  | 300 | За 3D-игрушки
10.02.2012 | пятница |  |  |  | 25 | Сверла 2 шт | Дюжина
16.02.2012 | четверг | 2500 | 3D-печать (макет бутылки)
24.02.2012 | пятница |  |  |  | 2400 | Оплата интернет-магазина printandplay.ru | Storeland.ru
25.02.2012 | суббота |  |  |  | 55 | Клей ПВА | Город
27.02.2012 | понедельник |  |  |  | 200 | Метизы (болты-гайки), ключи гаечные | СтройТоргСервис, Кутателадзе, 4
28.02.2012 | вторник | 2200 | 3D-печать (макет бутылки 2)
02.03.2012 | пятница |  |  |  | 2500 | Вернул долг Наговицину | Щ
 |  |  |  |  | 300 | Уровень Зубр | Абрис
06.03.2012 | вторник |  |  |  | 160 | Болты M8x60 50шт | ПУ-55
21.03.2012 | среда | 600 | Предоплата за модель (ventil)
27.03.2012 | вторник | 600 | Оплата за модель (ventil) |  | 400 | Оплата работы Леше | Щ
 |  |  |  |  | 200 | Плашка, плашкодержатель | Магазин Инструменты на Кутателадзе
29.03.2012 | четверг |  |  |  | 100 | Метчик на 8 чистовой | Магазин Инструменты на Кутателадзе
 |  |  |  |  | 100 | Метизы | Крепеж на Российской
30.03.2012 | пятница |  |  |  | 100 | Разьемы для электроники | Город
04.04.2012 | среда | 2600 | Печать модели (orca)
06.04.2012 | пятница | 2100 | Продажа пластика (1003)
08.04.2012 | воскресенье | 3200 | Печать модели (shkiv), продажа пластика (1002)
12.04.2012 | четверг |  |  |  | 230 | Ножовка по металлу, развертка на 8 | АкадемСнаб, Пасечная, 4
 |  |  |  |  | 1480 | Заказ двигателя у StepMotor.ru | Перевод через банк УралСиб
17.04.2012 | вторник |  |  |  | 280 | Винты, диоды, провода | Радиотехника, Крепеж
18.04.2012 | среда |  |  |  | 610 | Отправка деталей ЕМС Почтой (orca) | БЦ Петербург
26.04.2012 | четверг |  |  |  | 50 | Вентилятор 8 см | Квеста
01.05.2012 | вторник |  |  |  | 5000 | Зарплата Леше | Щ
29.05.2012 | вторник |  |  |  | 2300 | Покупка платы стола + доставка Пони Экспресс, оплата через Сбербанк-Онлайн | СКБ Кипарис
31.05.2012 | четверг |  |  |  | 2500 | Отдал долг Наговицину | Щ
08.06.2012 | пятница |  |  |  | 2500 | Сверлильный станок | Щ
14.06.2012 | четверг |  |  |  | 357 | Пинцет, теплопроводящая паста, длинногубцы, резисторы | Радиотехника
28.06.2012 | четверг |  |  |  | 2590 | Оплата за пластик для 3D-принтера | Альфа-клик
04.07.2012 | среда |  |  |  | 4000 | Зарплата Леше за апрель | Щ
09.07.2012 | понедельник |  |  |  | 975 | Оплата за доставку пластика ТК-КИТ | Щ
12.07.2012 | четверг | 4300 | Печать бутылок (bottle2, bottle3)
15.07.2012 | воскресенье | 3000 | Продажа пластика ABS
23.07.2012 | понедельник |  |  |  | 23 | Резисторы 8 Ом | Радиотехника
25.07.2012 | среда |  |  |  | 2867 | Шуруповерт, метчики, надфили | Дюжина
27.07.2012 | пятница | 800 | 3D-печать (домик Арбузову)
01.08.2012 | среда | 50000 | Продажа 3D-принтера + 2 кг пластика
06.08.2012 | понедельник |  |  |  | 1500 | БП 450 Вт | Квеста
14.08.2012 | вторник |  |  |  | 15500 | Оргстекло 18 мм 1400x1620 | ТД Пластик
 |  |  |  |  | 5670 | Оргстекло 8 мм 1500x1700 | ТД Пластик
 |  |  |  |  | 300 | Фторопласт 15 мм 1 м | Резинотехника
 |  |  |  |  | 825 | Фторопласт 25 мм 1 м | Резинотехника
 |  |  |  |  | 269 | Капролон 30 см 20x20 брусок 5 шт | Резинотехника
 |  |  |  |  | 350 | Газель грузовая 1 час | ТК Абсолют
16.08.2012 | четверг |  |  |  | 20000 | Зачисление на карточный счет (оплата направляющих на Alibaba.com) | Глобэкс-банк
17.08.2012 | пятница |  |  |  | 800 | Оплата отправки 2 кг ABS пластика (заказ 1005) ЕМС Почтой | Щ
20.08.2012 | понедельник |  |  |  | 2650 | 50 подшипников для принтера | Академснаб
29.08.2012 | среда |  |  |  | 2584 | Метизы для 5 принтеров | Крепеж на Иванова 31
05.09.2012 | среда |  |  |  | 2000 | Лазерная резка (четвертование + комплект на 1 принтер) | Мазак-лазер
07.09.2012 | пятница |  |  |  | 400 | Визитки 300 шт | Абвей, Демакова, 23
11.09.2012 | вторник |  |  |  | 2000 | 10 нагревательных элементов для 3D-принтеров | Щ
19.09.2012 | среда |  |  |  | 4216 | Пластик ABS 9.37 кг | Альфа-клик
 |  |  |  |  | 3315 | 2 муфты от СКБ ИС | Альфа-клик
20.09.2012 | четверг |  |  |  | 1673 | Метчики на 5, метчикодержатель, шлифмашинка электр. | Дюжина
21.09.2012 | пятница |  |  |  | 552 | Патрон конус 16 макс диаметр 16, сверло 15 мм, ключ на 17 | Дюжина
 |  |  |  |  | 5500 | Оплата резки оргстекла | Мазак-лазер
25.09.2012 | вторник |  |  |  | 1000 | Оплата за 20 втулок из капролона (материал дал я) | Виталий токарь, Щ
27.09.2012 | четверг | 3500 | Получил за ABS-пластик 7 кг (1007)
29.09.2012 | суббота |  |  |  | 1690 | Оплата отправки ABS-пластика ЕМС почтой | Щ
09.10.2012 | вторник | 800 | 3D-печать (jeep_disc)
13.10.2012 | суббота |  |  |  | 1848 | DFRduino Mega + драйвер ШД EasyDriver 4.4 | Devicter.ru
16.10.2012 | вторник |  |  |  | 570 | Набор для паяльных работ, провод МГТФ 2м, клеммы | Радиотехника
17.10.2012 | среда |  |  |  | 35 | PBS-40 PLS-40 разъемы | Радиотехника
22.10.2012 | понедельник |  |  |  | 3000 | Направляющие 40 шт 8x400мм, 2м пруток 10мм | ООО Скат, Зеленая горка, 1
23.10.2012 | вторник | 400 | Дима вернул за пруток 10мм
25.10.2012 | четверг | 4300 | Оплата ABS-пластика 4 кг
29.10.2012 | понедельник |  |  |  | 88 | Гайки переходные М8 6 шт (по 9р30к), щетка | Крепеж
30.10.2012 | вторник |  |  |  | 1290 | Отправка ABS-пластика ЕМС-почтой | Щ
11.11.2012 | воскресенье | 1000 | ABS-пластик 1 кг
14.11.2012 | среда |  |  |  | 370 | Гайки переходные 40 шт | Крепеж
16.11.2012 | пятница | 500 | Перевод с WM (вебинар donate)
24.11.2012 | суббота |  |  |  | 9094 | Оплата 20 кг ABS-пластика 3мм | Альфа-клик
06.12.2012 | четверг |  |  |  | 1000 | Оплата доставки 20 кг ABS-пластика | Щ
07.12.2012 | пятница | 800 | Продал 1 кг ABS-пластика
24.12.2012 | понедельник |  |  |  | 54 | Метизы | Крепеж
30.12.2012 | воскресенье | 860 | Продал комплектующие для 3d-принтера в НГТУ
08.01.2013 | вторник | 1900 | Продал 2 кг ABS пластика (бесцветного)
09.02.2013 | суббота |  |  |  | 184 | Электронные компоненты | Электронщик ул Нарымская
15.02.2013 | пятница | 1400 | Продал 2 подставки под микрофон
19.02.2013 | вторник |  |  |  | 1350 | Оплата интернет-магазина printandplay.ru через Альфа-клик и WM | Альфа-клик и WM
07.03.2013 | четверг | 1920 | ABS пластик 1 кг красного + 1 кг белого (1013)
11.03.2013 | понедельник | 1600 | Белый ABS 2 кг
20.03.2013 | среда |  | поступила предоплата 20000 на сберкарту за 3d-принтер
22.03.2013 | пятница |  |  |  | 2500 | Монитор б/у 19 дюймов Philips 190S | Форум Академгородка
25.03.2013 | понедельник |  |  |  | 350 | Сетевой фильтр 5 розеток 3 метра провод | Кольцово
26.03.2013 | вторник |  |  |  | 2070 | Оплата SMD светодиодов, NTC термисторов и R для столов по 100 шт | ЧипДип
28.03.2013 | четверг | 20000 | Предоплата за 3D-принтер от Лесникова А.В. |  | 20392 | Оплата 19 двигателей NEMA 17 и 20ти муфт + доставка ЕМС почтой 1820 руб | Darxton.ru
 |  |  |  |  | 204 | 1% за перевод Сбербанку | Сбербанк
01.04.2013 | понедельник | 5500 | Предоплата за 3D-принтер от Лесникова А.В. |  | 409 | Канифоль, припой, 5м силикон провода 1мм (245р), клеммы 20шт (60р) | Радиотехника, Иванова, 17
 |  |  |  |  | 6282 | Оплачено 25 NTC термисторов проволочных EPCOS B57560G104F +300C по 215.28р + доставка 900р | elitan.ru
 |  |  |  |  | 5500 | Оплачено 20 сопел для 3D-принтера в Барнаул Беликову Евгению | Сбербанк онлайн
 |  |  |  |  | 38 | 2 ключа шестигранника на 2,5 мм | Крепеж, Иванова, 31
03.04.2013 | среда |  |  |  | 456 | 6 стекол 210x210x4мм | Резка зеркал, Иванова, 31
04.04.2013 | четверг |  |  |  | 141 | Шило, сверло 4.5, проволока для стяжек | Дюжина
 |  |  |  |  | 347 | Винты М6, метчики, ключ шестигранник 5 | Крепеж, Иванова, 31
06.04.2013 | суббота |  |  |  | 1000 | Оставил на покупку радиодеталей в НГТУ | НГТУ
 |  |  |  |  | 100 | Дощечки 12x18 см 10 шт | Валерий, Щ
08.04.2013 | понедельник |  |  |  | 1500 | Оплата штрафа за направляющие | Альфа-клик
12.04.2013 | пятница |  |  |  | 300 | Оплата доставки посылки от ЧипИДип Автотрейдингом | Щ
 |  |  |  |  | 2985 | Оплата 10 м ремней компании АБЕЛТ | Альфа-клик
13.04.2013 | суббота |  |  |  | 1740 | RAMPS-плата + радиатор вместо тестовой | Devicter
16.04.2013 | вторник | 800 | Продал 1 кг красного ABS-пластика
18.04.2013 | четверг |  |  |  | 2525 | 5 SATA кабелей + Веб-камера Logitech B910 HD 5 Mpix | e2e4online.ru
20.04.2013 | суббота |  |  |  | 540 | Электронные компоненты | Электронщик, Горский м-н, 61
24.04.2013 | среда |  |  |  | 10736 | Оплата изготовления плат стола через Альфа-клик | Электроконнект
 |  |  |  |  | 1374 | Оплата 20 шт MOSFET STP55NF06L через WM | Элитан
 |  |  |  |  | 225 | 5 метровых шпилек M8 | Крепеж
 |  |  |  |  | 790 | БП LinkWorld LW2-500W | e2e4online.ru
25.04.2013 | четверг |  |  |  | 7011 | Оплата изготовления плат стола через Альфа-клик | Электроконнект
26.04.2013 | пятница |  |  |  | 125 | PBS-40R разъемы 5шт | Радиотехника
 |  |  |  |  | 235 | Лупа с зажимом Третья рука | Радиотехника
 |  |  |  |  | 297 | Бокорезы | Радиотехника
 |  |  |  |  | 36 | Термообжим | Радиотехника
 |  |  |  |  | 200 | Провода 4х цветов по 10 метров | Радиотехника
 |  |  |  |  | 20 | Винты с потайной головкой M4x35 20шт | Крепеж
02.05.2013 | четверг |  |  |  | 112 | Сверло 2,5 мм, 16 мм | Дюжина
04.05.2013 | суббота |  |  |  | 2502 | Оплата монтажа плат САНТ | Альфа-клик
05.05.2013 | воскресенье | 500 | Продал 2 кг ABS серого за печать деталей
08.05.2013 | среда |  |  |  | 33 | Клей Grifon | Авоська, Кольцово
 |  |  |  |  | 110 | Полотно для шлицовки, биты на 4,5 мм внутр. шестигранник для шуруповерта, магнитный держатель | Дюжина
 |  |  |  |  | 320 | 1.2 мм хвостовик 0.26 мм 10 шт HSCO комплект сверл | АкадемСнаб
 |  |  |  |  | 200 | 1.2 мм хвостовик 0.5 мм 10 шт комплект сверл | АкадемСнаб
13.05.2013 | понедельник |  |  |  | 315 | Шпильки M8 1м 7 штук | Крепеж
17.05.2013 | пятница | 2000 | Оплата контроля сделки по 3D-принтеру ReplicatorG
 |  | 200 | Продажа сверл Сереге
 |  | 150 | Продажа сверл Ивану
22.05.2013 | среда | 500 | Продал Диме 1,5 м ремня Т5 и кольцевой ремень
25.05.2013 | суббота |  |  |  | 860 | Электронные компоненты | Электронщик
 |  |  |  |  | 200 | Предоплата за 5 пар 26pin разъемов | Электронщик
28.05.2013 | вторник |  |  |  | 3000 | Оплата Freeduino + 4 StepStick с радиаторами | devicter.ru
05.06.2013 | среда | 5000 | Предоплата за принтер от Лесникова
06.06.2013 | четверг |  |  |  | 334 | Мебельные болты с гайкой, наушники защитные, очки защитные 2 шт | Крепеж
07.06.2013 | пятница | 6800 | Предоплата за принтер от Лесникова
09.06.2013 | воскресенье | 800 | ABS пластик красный 1 кг
10.06.2013 | понедельник |  |  |  | 200 | Два сломанных БП с вентиляторами 12 см | Пос. РМЗ
13.06.2013 | четверг | 550 | Дима купил 2 муфты
14.06.2013 | пятница |  |  |  | 22 | Клей Grifon | Авоська
16.06.2013 | воскресенье | 300 | Продал терморезистор Ивану
17.06.2013 | понедельник |  |  |  | 678 | Гайки M4 с нейлон. вст 50 шт, 2 ключа M4, рулетка 3 м, клей 3 шт, винты M3x12 50 шт, ножи технич 2 шт, биты для шуруповерта | Крепеж
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

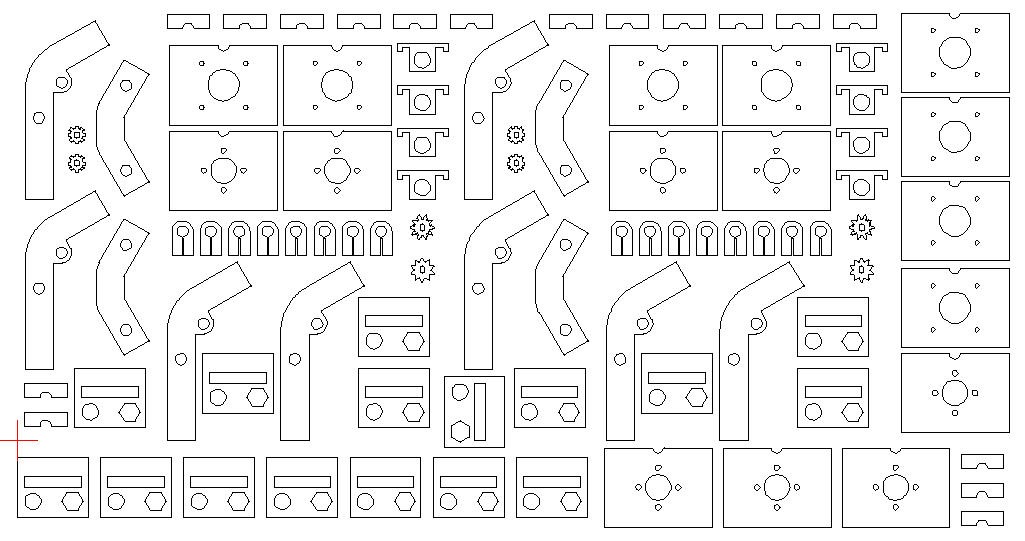
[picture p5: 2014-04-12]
sibrap/laserblocks/parts18_final_14mm_feb2014.png

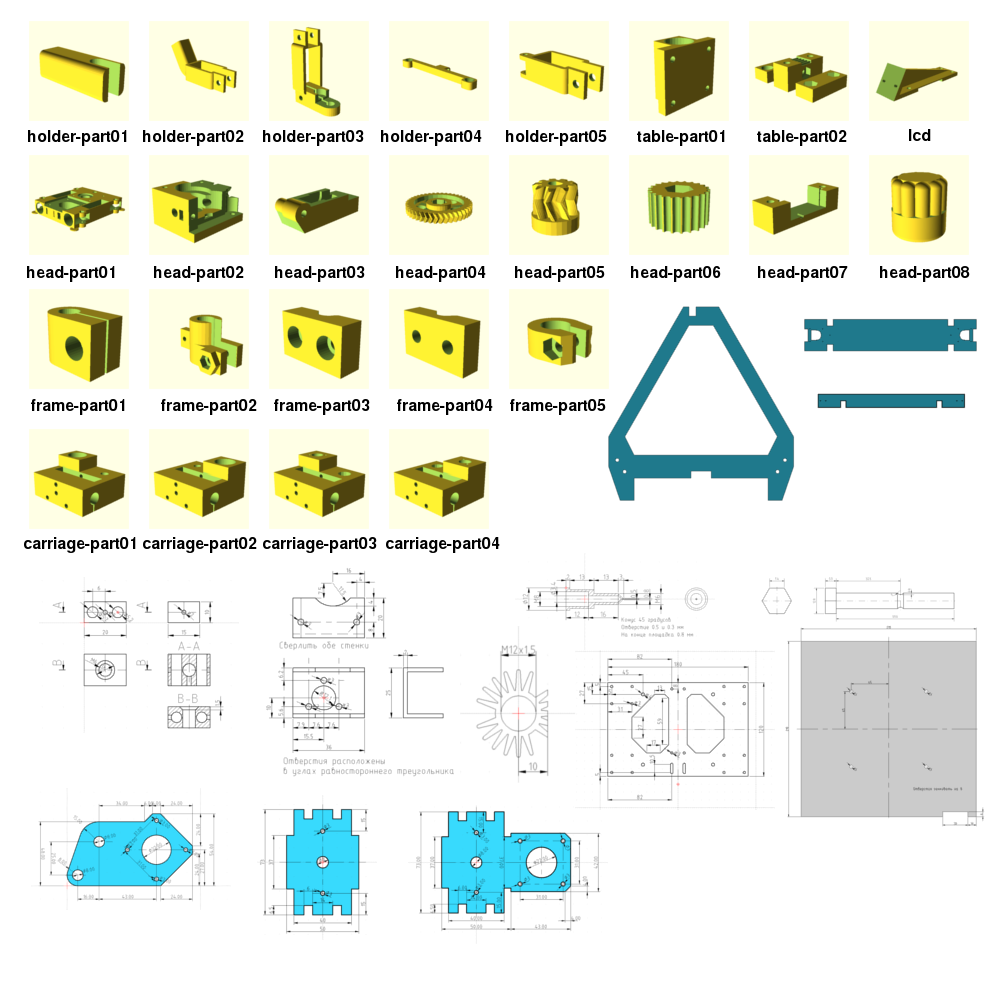
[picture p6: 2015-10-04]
sibrap/sibrap-parts-3.png

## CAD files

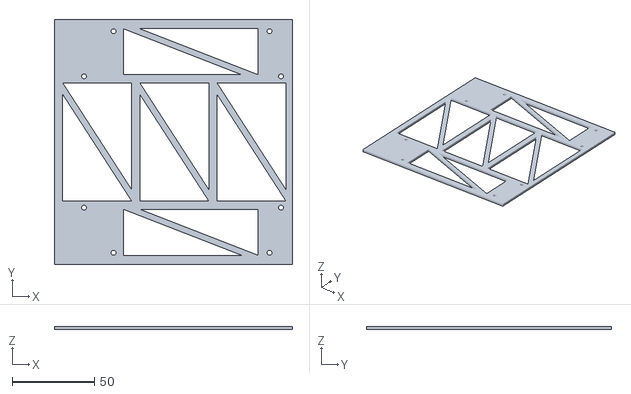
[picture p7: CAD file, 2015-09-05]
bonus/int1.stl
145.0 x 149.0 x 2.00

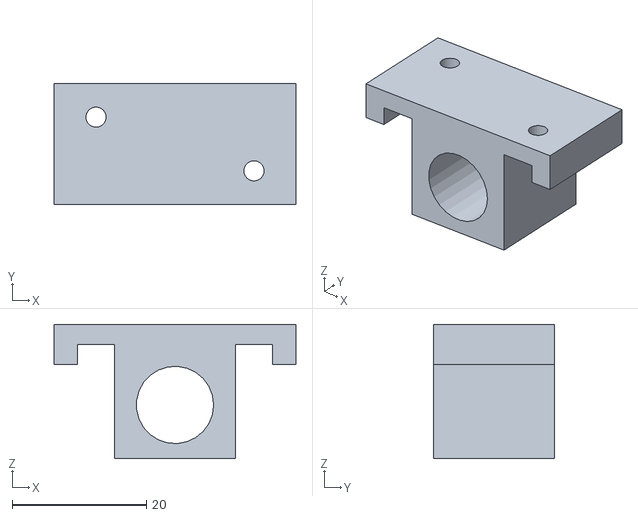
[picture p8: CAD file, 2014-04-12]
export/part22.stl
36.0 x 18.0 x 20.0

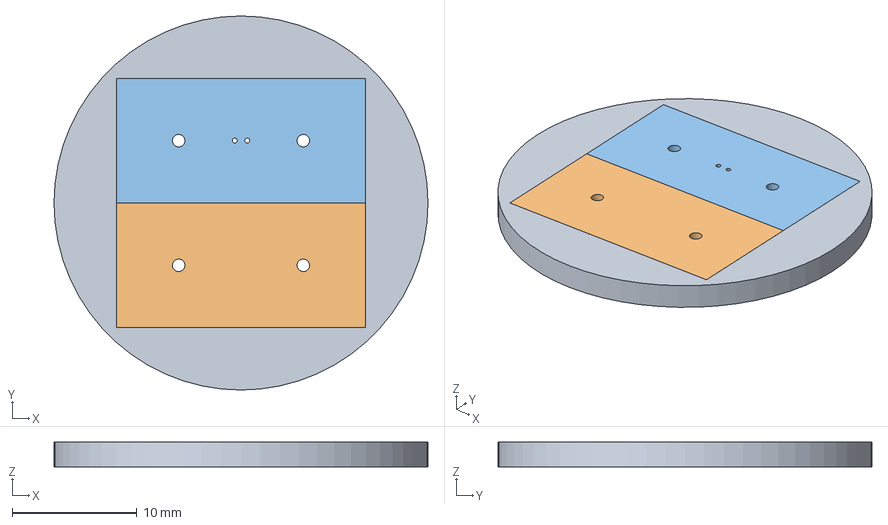
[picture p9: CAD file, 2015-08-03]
ftoroplast.FCStd
30.0 x 30.0 x 2.00 mm

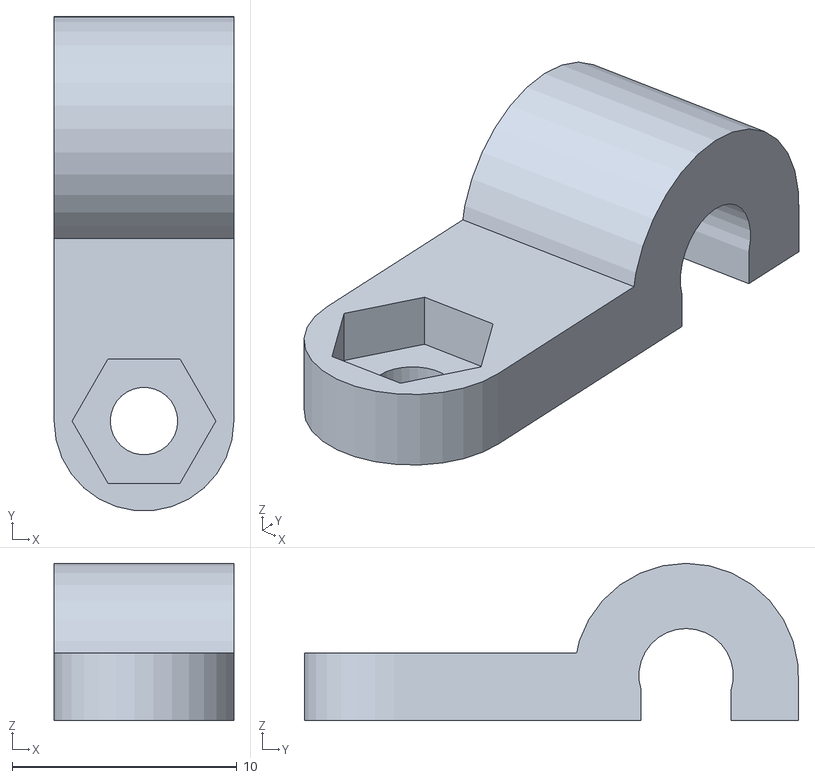
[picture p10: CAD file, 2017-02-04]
sibrap/abs/stl/holder-tube.stl
8.00 x 22.0 x 7.00

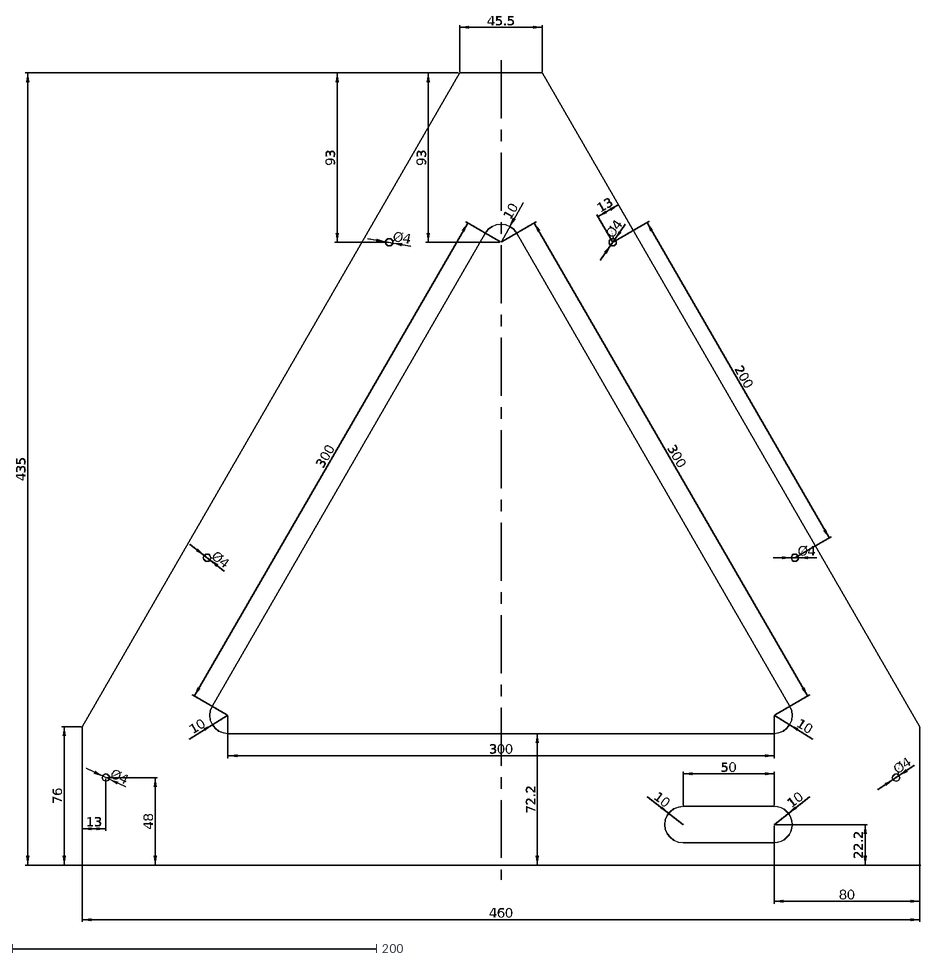
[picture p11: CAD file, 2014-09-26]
sibrap/case/part2.dxf
435
76
10
45.5
50
460
13
Ø4
300
200
93
48
22.2
80
72.2

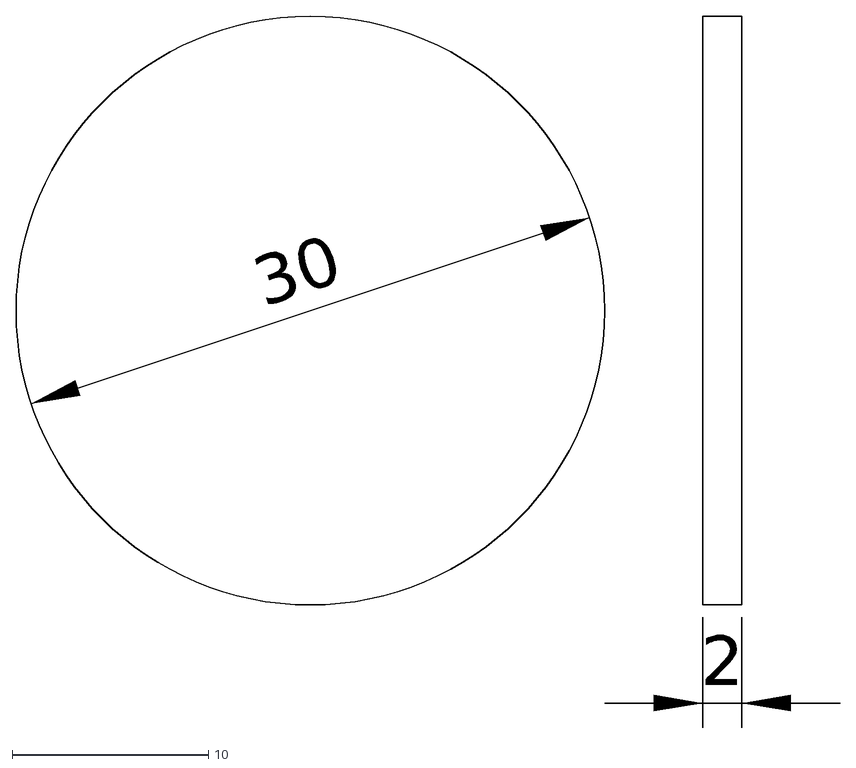
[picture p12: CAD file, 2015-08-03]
sibrap/ftoroplast/extruder-part08.dxf
30
2

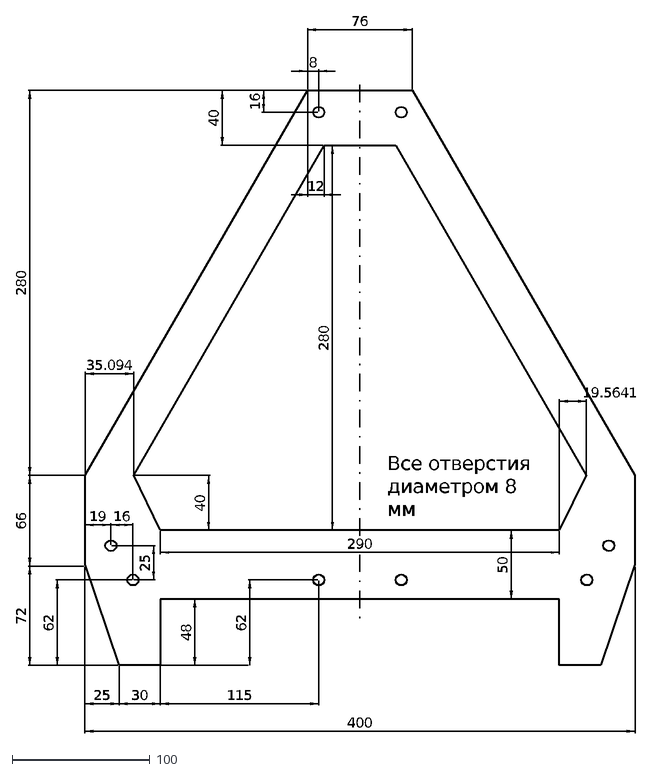
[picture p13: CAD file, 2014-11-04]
sibrap/laser/frame/frame.dxf
76
280
66
72
48
62
25
16
40
8
19
30
400
19.5641
290
115
35.094
12
50
Все отверстия диаметром 8 мм

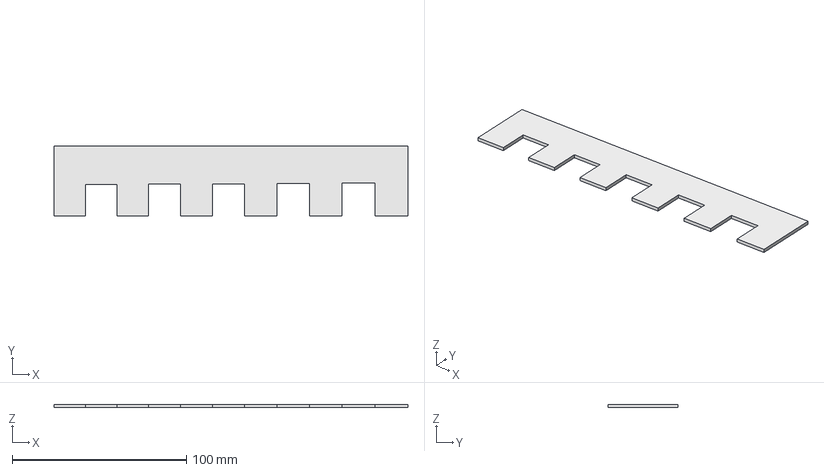
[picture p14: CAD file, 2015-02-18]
sibrap/laser/frame/v3/test.fcstd
203.0 x 40.0 x 2.00 mm

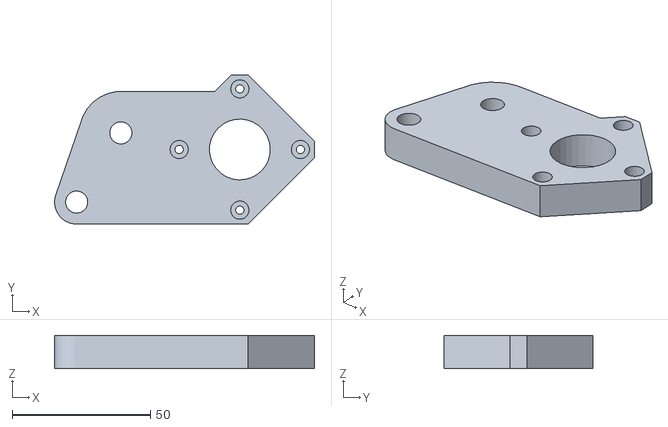
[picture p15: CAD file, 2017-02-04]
sibrap/laser/part13.stl
94.0 x 54.0 x 12.0

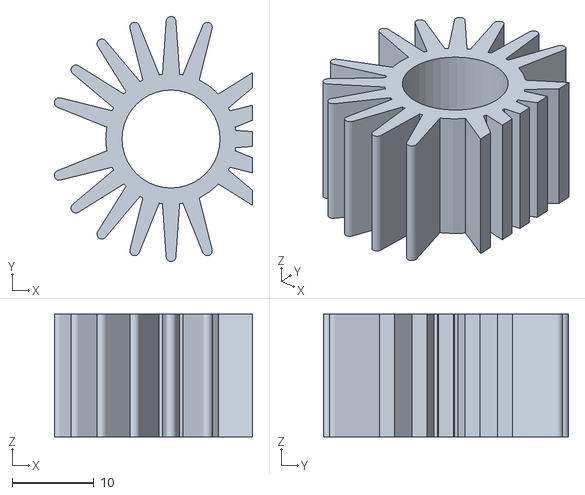
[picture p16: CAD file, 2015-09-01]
sibrap/metal/alum_radiator/radiator.stl
24.3 x 30.0 x 15.0

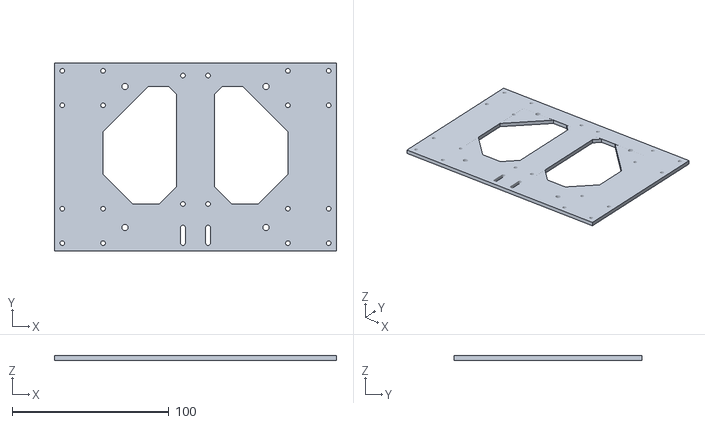
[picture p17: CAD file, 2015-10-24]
sibrap/metal/alum_table/table-3mm-aluminium.stl
180.0 x 120.0 x 3.00

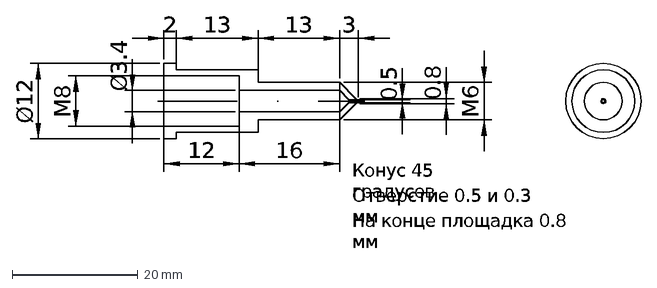
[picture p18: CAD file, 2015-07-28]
sibrap/metal/extruder-part05.dxf
2
13
3
12
16
0.5
0.8
Ø3.4
M8
M6
Конус 45 градусов
Отверстие 0.5 и 0.3 мм
На конце площадка 0.8 мм
Ø12

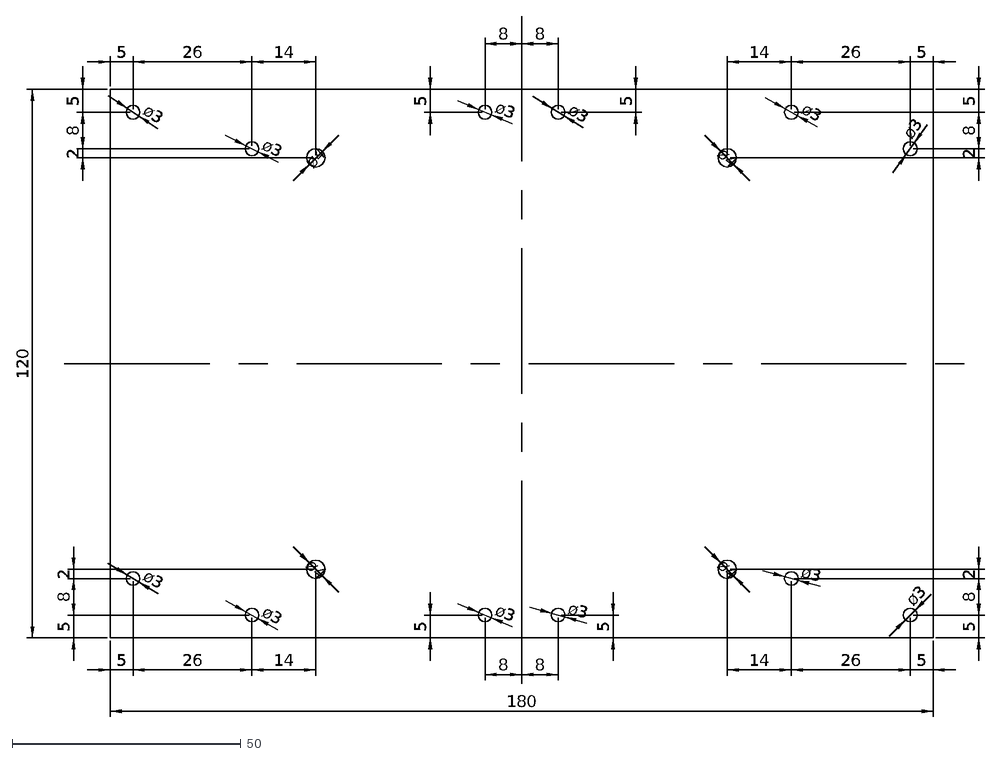
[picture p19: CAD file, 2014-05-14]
sibrap/table/table1.dxf
ø3
ø4
8
120
180
5
26
14
2

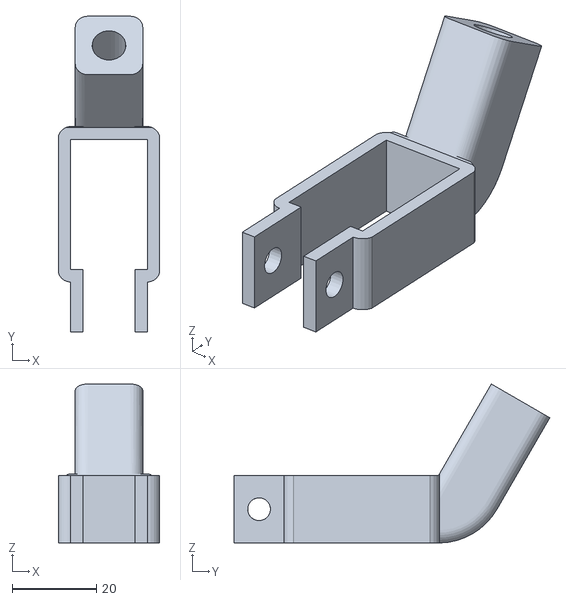
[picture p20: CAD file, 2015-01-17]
sibrap/v1_4/spool_vent_holder/d2-v2-rotated.stl
24.0 x 74.7 x 37.7

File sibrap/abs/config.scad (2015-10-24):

/**
 * Глобальный конфигурационный файл
 */
// качество цилиндров
$fn=30;

// избегание совпадения граней
DELTA=0.1;

// толщина рамы
FRAME=18;

// расстояние от стенок до гайки
DELTA_NUT = 0.3;
// высота, макс. диаметр, между стенками (размер ключа)
// гайка М3
m3_base=[2.4,6.4,5.5];
m3_hole=m3_base+[DELTA_NUT,DELTA_NUT,DELTA_NUT];
//[3,7,6]
// гайка М4
m4_base=[3.2,8.1,6.9];
m4_hole=m4_base+[DELTA_NUT,DELTA_NUT,DELTA_NUT];
// гайка М5
m5_base=[3.8,9.1,7.9];
m5_hole=m5_base+[DELTA_NUT,DELTA_NUT,DELTA_NUT];

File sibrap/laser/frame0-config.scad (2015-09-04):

// Рама для 3д-принтера SibRap
// под любую толщину оргстекла
// Генерируются чертежи в dxf-формате

// толщина оргстекла
dh = 18;
// качество цилиндров
$fn = 30;
// качество цилиндров для мелких отверстий
fn2 = 10;
// диаметр отверстий меньше этого будет 1 мм при раскрое
D_MIN = 6;

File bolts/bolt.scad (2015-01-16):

use <din_bolts.scad>
//use <MCAD/metric_fastners.scad>

// DIN 7985
// http://www.tdm-neva.ru/screws/din-7985-vint.htm
// DIN 912
// http://www.tdm-neva.ru/screws/din-912-vint.htm

sizes=[10,12,16,20,25,30,35,40,50,60];
//metric=[3,4,5,6,8];
//sizes=[10,12,16,20,25];
//sizes=[30,35,40,50,60];
metric=[5];

k=0;
l=0;
for(s=sizes) {							
	for(m=metric) {
		translate([(s-10)*10,(m-3)*20,0])inhex_bolt(m,s);
	}
}

//inhex_bolt(8,20);

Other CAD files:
sibrap/laserblocks/parts8_dec2014_final.dxf
bonus/int2.stl
export/part21.stl
sibrap/abs/stl/lcd1.stl
bolts/din_bolts.scad
bolts/bolt.stl
bolts/flange_nut.scad
bolts/flange_nut.stl
bolts/flange_nut/m10_fl_nut.stl
bolts/flange_nut/m12_fl_nut.stl
bolts/flange_nut/m14_fl_nut.stl
bolts/flange_nut/m16_fl_nut.stl
bolts/flange_nut/m20_fl_nut.stl
bolts/flange_nut/m5_fl_nut.stl
bolts/flange_nut/m6_fl_nut.stl
bolts/flange_nut/m8_fl_nut.stl
bolts/inhex/m5x10_ih.stl
bolts/inhex/m5x12_ih.stl
bolts/inhex/m5x16_ih.stl
bolts/inhex/m5x20_ih.stl
bolts/inhex/m5x25_ih.stl
bolts/inhex/m5x30_ih.stl
bolts/inhex/m5x35_ih.stl
bolts/inhex/m5x40_ih.stl
bolts/inhex/m5x50_ih.stl
bolts/inhex/m5x60_ih.stl
bolts/m3x10_cr.stl
bolts/m3x12_cr.stl
bolts/m3x16_cr.stl
bolts/m3x20_cr.stl
bolts/m3x25_cr.stl
bolts/m3x30_cr.stl
bolts/m3x35_cr.stl
bolts/m3x40_cr.stl
bolts/m3x50_cr.stl
bolts/m3x60_cr.stl
bolts/m5x10_cr.stl
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

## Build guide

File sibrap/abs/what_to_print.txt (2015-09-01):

Печатать нужно

base_plate01
base_plate02
base_plate03
base_plate04
carriage-part01
carriage-part02
carriage-part03
carriage-part04
head-part01
head-part02
head-part04

по 1 шт

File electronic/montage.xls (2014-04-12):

Настоящая Заявка является неотъемлемой частью счет-договора
Факсимильная копия настоящей заявки имеет силу оригинала.
Выделенные желтым цветом поля шапки заказа должны быть обязательно заполнены
Заявка на монтаж печатных плат |  |  |  |  |  |  | Дата заявки |  | 2013-04-12
Заказчик (название фирмы, предприятия) |  |  |  |  | Нуждов Андрей Александрович
ИНН/КПП: |  | - |  |  |  | E-mail: |  | mail@answe.ru
Адрес |  | ул. Иванова 38-185
Ф.И.О., телефоны/факсы контактных лиц, включая код города |  |  | По тех. вопросам |  | 79232464120
 |  |  | По орг. вопросам
 |  |  | По доставке
Задание на монтаж и комплектацию
Тип заказа (новый, повторный) |  |  |  | Новый
Номера заказов (PS……) |  |  |  | -
Имя файла платы |  |  |  | table9.lay
Формат файла платы |  |  |  | Sprint Layout 5.1
Количество плат |  |  |  | 50
Точные размеры платы (мм.) |  |  |  | 210x210
Толщина платы (мм.) |  |  |  | 1.5
Монтаж одно- или двухсторонний |  |  |  | Односторонний
Влагозащита |  |  |  | Не нужна
Отмывка |  |  |  | Не нужна
Комплектация заказа |  |  |  | Не нужна
Данные на одну плату
Количество паек SMD |  |  |  | 6
Количество паек в отверстия |  |  |  | 6
!!! Наличие RoHS компонентов * |  |  |  | Нет
Компоненты с точным простран- |  |  |  | 0
ственным положением ** |  |  |  | 1
Механические детали |  |  |  | 0
Облуживание проводов |  |  |  | 0
Плотность монтажа |  |  |  | 6
Наличие реперных знаков |  |  |  | Нет
Доставка
Доставка осуществляется ООО «САНТ» (да/нет, указать пункт назначения)
Иное:
* Монтаж плат осуществляется с применением свинцовосодержащей пасты. В случае ответов "Да" и "Не знаю" будет примеменен специальный тип паяльной пасты, гарантирующий надежность пайки бессвинцовых компонентов. При этом стоимость монтажа увеличивается на 10%. Если в этой графе укзано "Нет" надежность пайки бессвинцовых компонентов не гарантируется.
** Например светодиод, корпус котороого расположен на высоте 5-и мм. над поверхностью платы, это компонент с 1-й пространственной координатой. Если, например выводы того же светодиода имеют загиб на 90 градусов на высоте 5-и мм. над поверхностью платы и корпус светодиода расположен в 4 мм. от этого загиба - компонент с 2-мя пространственными координатами.
 | Подпись заказчика
 |  | М.П.

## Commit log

2014-04-12 initial commit to GitHub
    [!!!!!!!_AJGW-GearsHering_2x_big.scad, !!!!!!!_AJGW-GearsHering_2x_small.scad, 10gear.dxf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]
2014-04-12 added ftoroplast detail
    [ftoroplast.FCStd]
2014-05-27 spool holder added
    [tst.scad, tst.stl, tst2.stl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]
2014-09-26 major update: - we moved to M5 threads on Z axis - we use radiator and increase speed - we use LM8UU instead of bronze bushing
    [1-rightbottom.scad, 1-rightbottom.stl, 2-leftbottom.scad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]
2014-10-31 docs updated
    [3dprinter-real.ods, 3dprinter-stats.ods]
2014-11-04 SibRap FreeCad project updated with new parts: - frame - belt - LM8UU - table - coupling
    [1-rightbottom.scad, 3-righttop.scad, frame.dxf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]
2014-11-04 sklad added
    [sibrap-10-sklad.ods]
2014-11-13 project updated
    [part06_new.scad, part06_new.stl]
2014-11-14 project updated
    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
    [part06.scad, part06_1.scad, part06_1.stl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]
2014-11-14 table is down
    [part12_gt2.scad, part12_gt2.stl]
2014-11-15 update
    update
    [sibrap-fullset.ods]
2014-11-17 frame updated
    [balka_bottom.dxf, balka_top.dxf, frame_final.dxf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]
2014-11-22 metal head added
    metal head added
    [part12.scad, part12.stl, part12_gt2.stl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]
2014-11-30 new molex part added
    new molex part added
    [part16.scad, part16_molex.scad, part16_molex.stl]
2015-01-05 new frame design added
    [all.dxf, frame_final_2.dxf, frame_final_3.dxf]
2015-01-07 freecad project updated
    [radiator.scad, radiator.stl]
2015-01-08 bolts added to project
    [bolt.scad, bolt.stl, cross_bolt.scad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]
2015-01-16 project bolts updated
    [barashek.stl, bolt.scad, cross_bolt.scad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]
2015-01-17 spool, vent holder added
    [d1-v3-rotated.stl, d2-v2-rotated.stl, d3-double.stl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]
2015-01-17 new bottom part added
    [balka_bottom_v2.dxf, balka_bottom_v2_1.dxf]
2015-01-18 flange nuts added
    [flange_nut.scad, flange_nut.stl, m10_fl_nut.stl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]
2015-01-19 provod updated
    [sibrap-provod-v1-4.ods]
2015-02-06 ramps box updated
    [ramps14-box-1.stl, ramps14-box-2.stl, ramps14-box.scad]
2015-02-06 laser parts updated
    [bottom_block.dxf, bottom_result.dxf, bottom_result2.dxf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]
2015-02-18 frame update, endstop update
    [final_sheet_1500_1700.dxf, part23.scad, test.dxf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]
2015-02-21 ramps box updated; sibrap label created
    [ramps14-box.scad]
2015-02-21 ramps box upgraded
    [ramps14-box-1.stl, ramps14-box-2.stl, ramps14-box.scad]
2015-07-25 - dimensions plugin added - some parts changed - kit specs added
    [TextGenerator.scad, dim.scad, dim_sample.scad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]
2015-07-25 Z endstop updated
    [halfcube.scad, part23.stl, part23_z1.scad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]
2015-07-31 dynamic frame added
    [frame-final.dxf, frame-final2.dxf, frame.scad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]
2015-09-01 abs parts major update: now you can generate them
    [1-rightbottom.scad, 1-rightbottom.stl, 10gear.dxf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]
2015-09-20 lcd display holder
    [lcd.scad, lcd.stl]
2015-10-24 z-regulated holder update
    [config.scad, frame-part02-z1.scad, frame-part02-z1.stl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]
2015-11-08 regulated table added
    [table-3mm-aluminium-regulated.scad]
2017-02-04 part13 updated
    [part13.scad, part13.stl]
2017-02-04 bowden (experimental) parts added
    [base-plate06.scad, head-part02-bowden.scad, head-part02-bowden.stl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]
